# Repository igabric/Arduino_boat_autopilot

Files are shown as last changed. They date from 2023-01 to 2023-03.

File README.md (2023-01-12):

# ARDUINO AUTOPILOT FOR SMALL BOATS - short description

This project was created with the goal of creating a low-cost device for automatic navigation using the arduino mega microcontroller interface. The picture shows the finished device with all parts installed in the control box. 4 buttons installed on the control box, 1 rotary encoder and a remote control with 4 buttons are used to set and control the device. Steering is provided by the use of a stepper motor and a threaded rod, which enables the steering wheel to be turned by approximately 5 degrees in each direction.



The power supply of the microcontroller and the stepper motor driver are separate. The main power source is the ship's batteries, which are charged using photovoltaic panels. The voltage on the accumulators is between 13 and 14 V which is fine for the stepper motor driver, but too high for the arduino microcontroller. Therefore, powermodule DC-DC 15-80 to 12V step-down power supply converter is used to power the microcontroller. Since the stepper motor driver is built into the control box, the heatsink part faces outwards to promote heat dissipation and reduce the heating of the microcontroller. The temperature in the control box is continuously controlled using a thermistor. In the event that the temperature exceeds a critical value (which can be adjusted in the device settings), an alarm is triggered and the operation of the stepper motor is disabled.The parts installed in the control box are shown in the picture:



# Settings and device management are achieved through the menu system shown in the images below.

## Init menu layout
Used for the initial positioning of the steering wheel and to setting the system.



## Main manu layout
Used for the function of anchoring, manual control and automatic control of the boat.



# Programming Arduino 

## Program flow diagrams
The simplified flow charts shown below are only a general indication of how the program works. The program modules contains a lot of details that significantly affect the functionality of the device.
  
### ** Main program flow diagram: **


### ** Initialization flow diagram: **


### ** Flow diagram for "manually" setting the neutral position of the rudder: **
Since the use of encoders is not provided for determining the initial position of the rudder, it is necessary to "manually" adjust the neutral position of the rudder before starting the automatic operation of the autopilot. 
  


### ** Flow diagram for system parameter settings: **
Note: The program enables the setting of more system parameters than shown in the flowchart.


### ** Flow diagram for autopilot main menu: **
The main menu consists of six possible choices, two of which are hidden. The most important functionalities are navigation according to the given course and navigation according to the given destination. Applying navigation to a set course does not take into account drift due to wind and sea currents, making the final destination unreliable. In this case, the autopilot tries to maintain the given course. By applying navigation to the destination (set longitude and latitude of the destination), the course is corrected during navigation, i.e. calculated based on the current position and the position of the destination. This method of navigation is reliable, and the error depends on the precision of the GPS device (for cheaper devices, it is of the order of 10 m).
The next functionality is the anchoring function. By calling this function at the moment of lowering the anchor, the current GPS position is recorded and the permitted deviation from the current position can be entered. If during the stay on the anchor there is a greater deviation than allowed (the anchor has loosened), an alarm (buzzer) is activated.
By starting the microcontroller, multiple points of interest (POIs) stored on the SD card are loaded. The program enables the entry of one custom POI that can be used within the navigation function to the destination (fourth function in the main menu).
The fifth hidden function refers to the manual control of the boat, which is achieved by pressing the button of the rotary encoder. Calling this function enables control using the buttons on the control box or using the remote control.
The sixth function refers to the return to the home menu.



### ** Flow diagram for anchoring function: **
Starting the anchoring function automatically records the current GPS location. Then the input of the permitted deviation from the current position is requested. After that, monitoring of the position on the anchor is started. A circle is drawn on the screen, the radius of which represents the permissible deviation from the anchoring location (center point). The current position is plotted on the LCD screen and refreshed every 5 seconds. If the distance of the current location from the anchoring location is greater than the permitted deviation, an alarm is activated.


### ** Flow diagram for input custom POI coordinates: **
Custom POI can be entered by entering two digits at a time to speed up coordinate entry. Coordinates are entered in decimal notation. Each entry must be confirmed by pressing the button on the rotary encoder. The program provides for the input of coordinates with 6 decimal places, although the flow diagram shows the input of only 4 decimal places.



### ** Flow diagram for navigation to destination (point of interest): **
Navigation towards the desired destination is done by first choosing a destination from the available database stored on the SD card or a custom POI that has been previously defined. After selecting the destination, the current location is read and the course towards the destination is calculated. If the speed of the boat is higher than the minimum required, which is defined in the program settings, it is checked whether the deviation of the current course from the budget is greater than the allowed tolerance. If the course deviation is greater, the rudder is turned in the appropriate direction. The process is repeated after 5 seconds. If the deviation of the course from the budget is less than allowed, the rudder returns to the neutral position. In the loop there is also the possibility to return to the main menu. In this way, the maximum precision of the navigation path is ensured, regardless of the wind and sea currents, because the course is recalculated every 5 seconds ("course over ground").



### ** Flow diagram for navigation to desired course: **
Navigation towards the desired direction (course) starts with entering the numerical value of the desired course. After that, the current GPS position (previous position) is read. Then there is a pause of 5 seconds after which the new current GPS position (next position) is loaded. Based on the two read positions, the current exchange rate is calculated. If the speed of the boat is higher than the minimum required (defined in the system settings), the current and desired course are compared. If the deviation is greater, the rudder is turned in the appropriate direction. Then the next position is declared as the previous position and the loop is repeated. If the deviation is less than allowed, the rudder returns to the neutral position. In the loop, it is possible to return to the main menu.



### ** Flow diagram for manual control: **
Starting the menu for manual control is done by pressing the button on the rotary encoder. This makes it possible to turn the rudder using the buttons on the device housing or using the remote control. The upper two buttons are used to gradually turn the rudder to the left or right, while pressing either of the lower two buttons returns the rudder to the neutral position. In the loop, it is possible to return to the main menu.



### ** Used components: **
1. TB6600 Single Axis 4A Stepper Motor Microstep Driver 9~40V Micro-Step - 1Pcs
2. Nema 23 Stepper Motor 3Nm/1.9Nm/1.26Nm 4-lead 2.8A/4.2A - 1Pcs
3. Beitian BN-800 Dual Module with Antenna Compass HMC5883L - 1Pcs
4. Mini 12mm Waterproof Momentary ON/OFF Push Button Round Switch - 4Pcs
5. 12mm Metal Push Button Switch Waterproof LED Light Momentary Latching - 1Pcs
6. 24V / 12V to 5V 5A powermodule DC-DC step-down power supply converter - 1Pcs
7. 315MHz/433MHz 4Buttons RF Remote Control - 1Pcs
8. 4 Channel 433MHz RF Wireless Remote Control Learning Decoding Receiver Module - 1Pcs
9. 3.2 Inch MEGA2560 Display Module HX8357B 480x320 TFT LCD Screen  - 1Pcs
10. 40 pcs Dupont Cables M-F Jumper Breadboard Wire GPIO Ribbon for connecting TFT LCD with Arduino MEGA - 1Pcs
11. MEGA 2560 R3 Arduino komp. Mikrokontroller Board Atmel ATmega2560  - 1Pcs
12. Several Dupont Cables M-F, M-M, F-F Jumper Breadboard Wire for wiring
13. NTC 3950 Thermistor 100KOhm  - 1Pcs
14. Resistor 100kOhm - 1Pcs
15. KY-040 Rotary Encoder Module - 1Pcs

### ** Wiring diagram: **


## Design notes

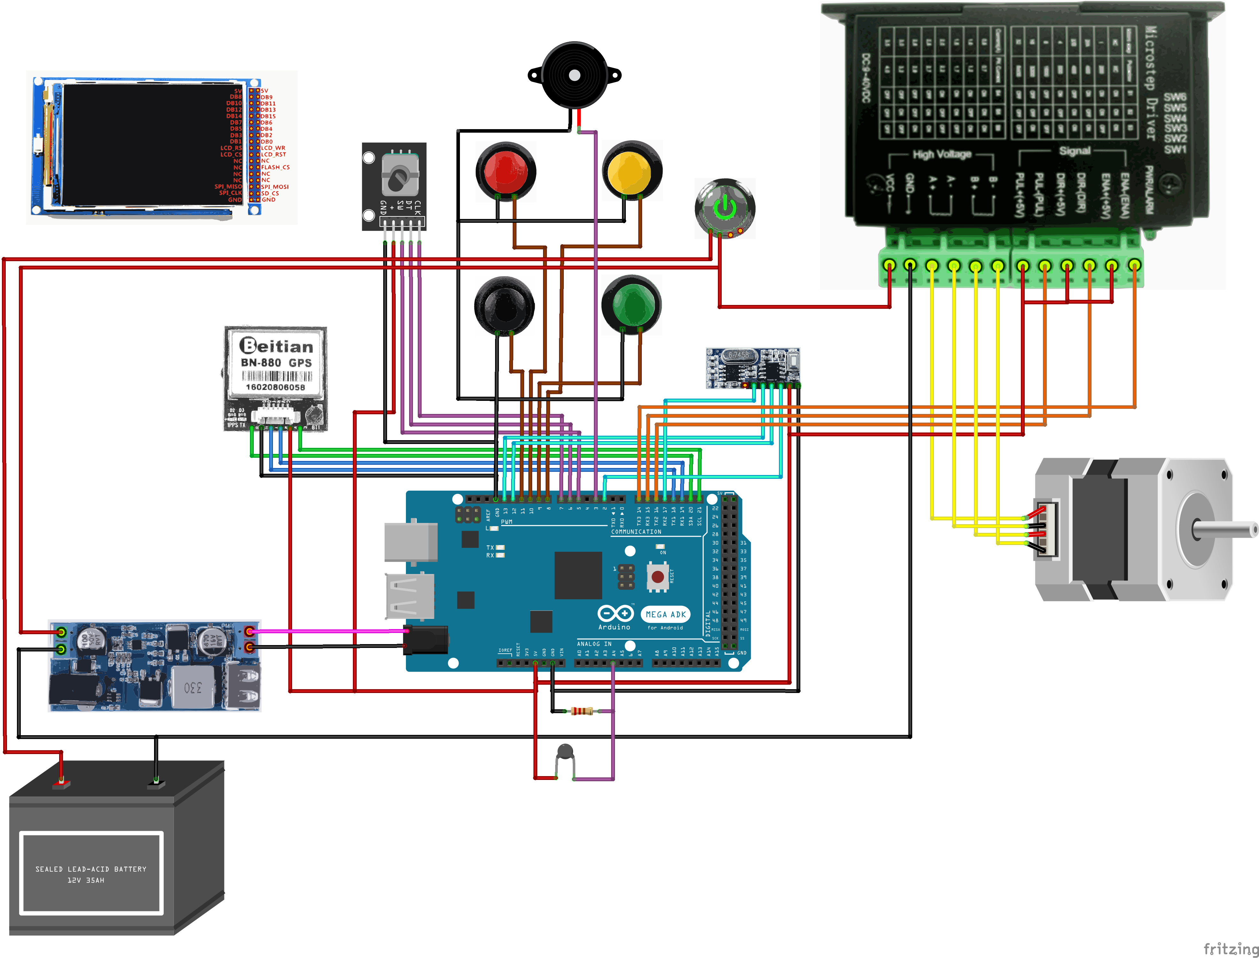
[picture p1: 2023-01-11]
Autopilot_shema.png

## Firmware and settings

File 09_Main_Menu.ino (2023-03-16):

void Screen_1_navigation(){
  int active_btn = 0;
  bool state = false;
  tft.fillScreen(TFT_BLACK);
  tft.drawRect(5, 5, 230, 150, TFT_YELLOW);
  tft.drawRect(245, 5, 230, 150, TFT_YELLOW);
  tft.drawRect(5, 165, 230, 150, TFT_YELLOW);
  tft.drawRect(245, 165, 230, 150, TFT_YELLOW);

  
  Set_Screen_1("Button 1", "Anchoring", 5, 5, false);
  Set_Screen_1("Button 2",  "Enter custom POI", 245, 5, false);
  Set_Screen_1("Button 3",  "Navigate by selected POI", 5, 165, false);
  Set_Screen_1("Button 4",  "Navigate by heading", 245, 165, false);
  TFT_print_entered_values();
  delay(1000);
  int prolaz_vrij = 0;
  while (true){
    prolaz_vrij += 1;
    if(prolaz_vrij == 2){
      temp = temperatura(); 
      tft.setTextColor(TFT_YELLOW, TFT_BLACK);
      tft.setCursor(410, 20, 4);
      tft.print(temp, 0);
      tft.setCursor(445, 20, 4);
      tft.print("C");
      prolaz_vrij = 0;
    }
    
    if(digitalRead(SW)== LOW){
      Manual_navigate();
    }
    if(digitalRead(PB_10p) == LOW and digitalRead(PB_1p) == LOW and digitalRead(PB_1n) == HIGH and digitalRead(PB_10n) == HIGH and digitalRead(SW)== HIGH){
      break;
    }
    if(digitalRead(PB_10n) == LOW){  
      Serial.println("Anchoring");
      if(active_btn == 1){
        state = 0; active_btn == 0;
        Set_Screen_1("Button 1", "Anchoring", 5, 5, false);
      }
      else if(active_btn == 2){
        Set_Screen_1("Button 2",  "Enter custom POI", 245, 5, false);
        Set_Screen_1("Button 1", "Anchoring", 5, 5, true);
        active_btn = 1; state = 1;
      }
      else if(active_btn == 3){
        Set_Screen_1("Button 3",  "Navigate by selected POI", 5, 165, false);
        Set_Screen_1("Button 1", "Anchoring", 5, 5, true);
        active_btn = 1; state = 1;
      }
      else if(active_btn == 4){
        Set_Screen_1("Button 4",  "Navigate by heading", 245, 165, false);
        Set_Screen_1("Button 1", "Anchoring", 5, 5, true);
        active_btn = 1; state = 1;
      }
      else{
        Set_Screen_1("Button 1", "Anchoring", 5, 5, true);
        active_btn = 1; state = 1;
      }
      delay(500);
    }
  if (digitalRead(PB_10n) == HIGH and digitalRead(PB_1n) == HIGH and digitalRead(PB_1p) == HIGH and digitalRead(PB_10p) == LOW and digitalRead(SW)== HIGH){
      Serial.println("Set POI");
      if(active_btn == 1){
        Set_Screen_1("Button 1", "Anchoring", 5, 5, false);
        Set_Screen_1("Button 2",  "Enter custom POI", 245, 5, true);
        active_btn = 2; state = 1;   
      }
      else if(active_btn == 2){
        state = 0; active_btn == 0;
        Set_Screen_1("Button 2",  "Enter custom POI", 245, 5, false);
      }
      else if(active_btn == 3){
        Set_Screen_1("Button 3",  "Navigate by selected POI", 5, 165, false);
        Set_Screen_1("Button 2",  "Enter custom POI", 245, 5, true);
        active_btn = 2; state = 1;
      }
      else if(active_btn == 4){
        Set_Screen_1("Button 4",  "Navigate by heading", 245, 165, false);
        Set_Screen_1("Button 2",  "Enter custom POI", 245, 5, true);
        active_btn = 2; state = 1;
      }
      else{
        Set_Screen_1("Button 2",  "Enter custom POI", 245, 5, true);
        active_btn = 2; state = 1;
      }
      delay(500);
    }
    if (digitalRead(PB_10n) == HIGH and digitalRead(PB_1n) == LOW and digitalRead(PB_1p) == HIGH and digitalRead(PB_10p) == HIGH and digitalRead(SW)== HIGH){
      Serial.println("Navigate by POI");
      if(active_btn == 1){
        Set_Screen_1("Button 1", "Anchoring", 5, 5, false);
        Set_Screen_1("Button 3",  "Navigate by selected POI", 5, 165, true);
        active_btn = 3; state = 1;   
      }
      else if(active_btn == 2){
        Set_Screen_1("Button 2",  "Enter custom POI", 245, 5, false);
        Set_Screen_1("Button 3",  "Navigate by selected POI", 5, 165, true);
        active_btn = 3; state = 1;
      }
      else if(active_btn == 3){
        state = 0; active_btn == 0;
        Set_Screen_1("Button 3",  "Navigate by selected POI", 5, 165, false);
      }
      else if(active_btn == 4){
        Set_Screen_1("Button 4",  "Navigate by heading", 245, 165, false);
        Set_Screen_1("Button 3",  "Navigate by selected POI", 5, 165, true);
        active_btn = 3; state = 1;
      }
      else{
        Set_Screen_1("Button 3",  "Navigate by selected POI", 5, 165, true);
        active_btn = 3; state = 1;
      }
      delay(500);
    }
    if (digitalRead(PB_10n) == HIGH and digitalRead(PB_1n) == HIGH and digitalRead(PB_1p) == LOW and digitalRead(PB_10p) == HIGH and digitalRead(SW)== HIGH){
      Serial.println("Navigate by heading");
      if(active_btn == 1){
        Set_Screen_1("Button 1", "Anchoring", 5, 5, false);
        Set_Screen_1("Button 4",  "Navigate by heading", 245, 165, true);
        active_btn = 4; state = 1;   
      }
      else if(active_btn == 2){
        Set_Screen_1("Button 2",  "Enter custom POI", 245, 5, false);
        Set_Screen_1("Button 4",  "Navigate by heading", 245, 165, true);
        active_btn = 4; state = 1;
      }
      else if(active_btn == 3){
        Set_Screen_1("Button 3",  "Navigate by selected POI", 5, 165, false);
        Set_Screen_1("Button 4",  "Navigate by heading", 245, 165, true);
        active_btn = 4; state = 1;
      }
      else if(active_btn == 4){
        state = 0; active_btn == 0;
        Set_Screen_1("Button 4",  "Navigate by heading", 245, 165, false);
      }
      else{
        Set_Screen_1("Button 4",  "Navigate by heading", 245, 165, true);
        active_btn = 4; state = 1;
      }
      delay(500);
    }
    
    if (state == 1){
      // CHOICE OF POIs BETWEEN OFFERED IN THE INTERNAL DATABASE
      if(active_btn == 1){ 
        Anchor_alarm();
        state = 0;
        Screen_1_navigation();
      }
      // ENTRY OF "CUSTOM" GEOGRAPHIC COORDINATES
      else if(active_btn == 2){
        // Enter custom POI coordinates
        number_of_POI = 26;
        pointArray[25] = "CUSTOM_POI";
        //Label(pointArray[arrLen], 200, 270, 4,"green");
        tft.setTextColor(TFT_YELLOW, TFT_BLACK);
        tft.setCursor(200, 270, 4);
        tft.print(pointArray[25]);
        rot_encoder_SET_CUSTOM_POI();
        longArray[25] = custom_POI_long;
        latArray[25] = custom_POI_lat;
         
        sign_custom_POI = true;
        state = 0;

        delay(1000);
        Screen_1_navigation();
      }
      // AUTOMATIC NAVIGATION by POINT OF INTEREST (POI)
      else if(active_btn == 3){
        // Navigate by selected POI 
        if (POI_selection != NULL){
          select_POI();
          state = 0;
          Autopilot_heading_POI(false);
          autopilot_ON = true;
          Navigate_by_POI();     
          delay(1000);
          Screen_1_navigation();
        }
        else{

          select_POI();         
          state = 0;
          autopilot_ON = true;
          Autopilot_heading_POI(false);
          Navigate_by_POI();     
          delay(1000);
          Screen_1_navigation();
        }
      }
      // AUTOMATIC NAVIGATION BY SELECTED HEADING
      else if(active_btn == 4){
        // Navigate by heading
        Autopilot_heading_POI(true);
        autopilot_ON = true;
        Autopilot(true);
        state = 0;
        Screen_1_navigation();
      }
    }
    delay(500);
  } 
  tft.fillScreen(TFT_BLACK);
}  


// ************************************************************************************************

//                                         Set_Screen_1 MODULE
//                                  SET ACTIVE BUTTON COLOUR ON SCREEN 1

// ************************************************************************************************
void Set_Screen_1(String text_btn, String description, int posx, int posy, bool active){
  if (active == true){
    tft.drawRect(posx, posy, 230, 150, TFT_WHITE);
    tft.setTextColor(TFT_WHITE, TFT_BLACK);
  }
  else{
    tft.drawRect(posx, posy, 230, 150, TFT_YELLOW);
    tft.setTextColor(TFT_RED, TFT_BLACK);
  }
  if (text_btn == "Button 1"){
    tft.fillCircle(posx + 115, posy + 40, 15, TFT_WHITE);
    tft.fillCircle(posx + 115, posy + 40, 12, TFT_RED);
  }
  else if (text_btn == "Button 2"){
    tft.fillCircle(posx + 115, posy + 40, 15, TFT_WHITE);
    tft.fillCircle(posx + 115, posy + 40, 12, TFT_YELLOW);
  }
  else if (text_btn == "Button 3"){
    tft.fillCircle(posx + 115, posy + 40, 15, TFT_WHITE);
    tft.fillCircle(posx + 115, posy + 40, 12, TFT_BLACK);
  }
  else if (text_btn == "Button 4"){
    tft.fillCircle(posx + 115, posy + 40, 15, TFT_WHITE);
    tft.fillCircle(posx + 115, posy + 40, 12, TFT_GREEN);
  }
  // tft.setCursor(posx + 30, posy + 50, 4);
  // tft.print(text_btn);
  tft.setCursor(posx + 30, posy + 80, 2);
  tft.print(description);
}
// ------------------------------------------------------------------------------------------------

// ************************************************************************************************

//                                    TFT_print_entered_values MODULE
//                               SHOW ON THE SCREEN 1 SELECTED/ENTERED VALUE 

// ************************************************************************************************
void TFT_print_entered_values(){
  if(custom_POI_long != NULL){
    tft.setTextColor(TFT_GREEN, TFT_BLACK);
    tft.setCursor(245 + 30, 5 + 100, 2);
    tft.print("Long:");
    tft.setCursor(245 + 30, 5 + 115, 2);
    tft.print("Lat:");
    tft.setTextColor(TFT_WHITE, TFT_BLACK);
    tft.setCursor(245 + 80, 5 + 100, 2);
    tft.print(custom_POI_long, 6); 
    tft.setCursor(245 + 80, 5 + 115, 2);
    tft.print(custom_POI_lat, 6);
  }
}
// ------------------------------------------------------------------------------------------------

void Manual_navigate(){
  digitalWrite(enablePin, HIGH); // enable stepper
  String buf1 = "000";
  tft.fillScreen(TFT_BLACK);
  tft.setTextColor(TFT_CYAN, TFT_BLACK);
  tft.setCursor(140, 40, 4);
  tft.println("MANUAL STEERING");
  tft.setCursor(20, 270, 4);
  tft.setTextColor(TFT_WHITE, TFT_BLACK);
  tft.println("Steering position:");
  drawRAW("kormilo_.raw", 215, 135, 50, 50);
  delay(1000);
  while (digitalRead(SW)== HIGH){
    tft.fillRect(270, 270, 50, 30, TFT_BLACK);
    buf1 = Leading_zero(STEPPER_MOTOR.getCurrentPositionInMillimeters(), 3);
    tft.setTextColor(TFT_YELLOW, TFT_BLACK);
    tft.setCursor(270, 270, 4);
    tft.print(buf1);
    if (digitalRead(PB_10p) == LOW and digitalRead(PB_1p) == HIGH and digitalRead(PB_1n) == HIGH and digitalRead(PB_10n) == HIGH and digitalRead(SW)== HIGH){
      // SET STEPPER CLOCKWISE
      sterring_positive();
    }
    else if(digitalRead(button1) == HIGH){
      // SET STEPPER COUNTERCLOCKWISE
      sterring_negative();
    }

    else if(digitalRead(button2) == HIGH){
      // SET STEPPER CLOCKWISE
      sterring_positive();
    }
    else if(digitalRead(PB_10p) == HIGH  and digitalRead(PB_1p) == HIGH and digitalRead(PB_1n) == HIGH and digitalRead(PB_10n) == LOW and  digitalRead(SW)== HIGH){
      // SET STEPPER COUNTERCLOCKWISE
      sterring_negative();
    }
    else if(digitalRead(PB_1p) == LOW or digitalRead(PB_1n) == LOW or digitalRead(button3) == HIGH or digitalRead(button4) == HIGH){
      tft.fillRect(220, 220, 40, 40, TFT_GREEN);
      // SET STEPPER NEUTRAL
      digitalWrite(enablePin, HIGH); // enable stepper
      temp = temperatura(); 
      STEPPER_MOTOR.moveToPositionInMillimeters(0);
      digitalWrite(enablePin, LOW); // disable stepper
      delay(500);
    }
    tft.fillTriangle(60, 160, 90, 140, 90, 180, TFT_BLACK);
    tft.fillTriangle(410, 160, 380, 140, 380, 180, TFT_BLACK);
    tft.fillRect(220, 220, 40, 40, TFT_BLACK);
    tft.setTextColor(TFT_BLACK, TFT_BLACK);
    tft.setCursor(135, 80, 4);
    tft.println("STEERING LIMIT !!!");
    digitalWrite(enablePin, LOW); // disable stepper
  }
  digitalWrite(enablePin, LOW); // disable stepper
  Screen_1_navigation();
}

void sterring_positive(){
  tft.fillTriangle(410, 160, 380, 140, 380, 180, TFT_GREEN);
  if(step_direction_positive == 1){
    if(STEPPER_MOTOR.getCurrentPositionInMillimeters()> -Max_steering_turning_deg){
      digitalWrite(enablePin, HIGH); // enable stepper
      temp = temperatura(); 
      STEPPER_MOTOR.moveRelativeInMillimeters(-10);
      // digitalWrite(enablePin, LOW); // disable stepper
    }
    else{
      tft.setTextColor(TFT_RED, TFT_BLACK);
      tft.setCursor(135, 80, 4);
      #ifdef DEBUG
        Serial.print("CurrentPositionInDegs: ");
        Serial.println(STEPPER_MOTOR.getCurrentPositionInMillimeters());
      #endif 
      tft.println("STEERING LIMIT !!!");
      delay(500);
    }
  }
  else{
    if(STEPPER_MOTOR.getCurrentPositionInMillimeters()<Max_steering_turning_deg){
      digitalWrite(enablePin, HIGH); // enable stepper
      temp = temperatura(); // 
      STEPPER_MOTOR.moveRelativeInMillimeters(10);
      // digitalWrite(enablePin, LOW); // disable stepper
    }
    else{
      tft.setTextColor(TFT_RED, TFT_BLACK);
      tft.setCursor(135, 80, 4);
      #ifdef DEBUG
        Serial.print("CurrentPositionInDegs: ");
        Serial.println(STEPPER_MOTOR.getCurrentPositionInMillimeters());
      #endif 
      tft.println("STEERING LIMIT !!!");
      delay(500);
    }
  }
}

void sterring_negative(){
  tft.fillTriangle(60, 160, 90, 140, 90, 180, TFT_GREEN);
  if(step_direction_positive == 1){
    if(STEPPER_MOTOR.getCurrentPositionInMillimeters()<Max_steering_turning_deg){
      digitalWrite(enablePin, HIGH); // enable stepper
      temp = temperatura();
      STEPPER_MOTOR.moveRelativeInMillimeters(10);
      // digitalWrite(enablePin, LOW); // disable stepper
    }
    else{
      tft.setTextColor(TFT_RED, TFT_BLACK);
      tft.setCursor(135, 80, 4);
      #ifdef DEBUG
        Serial.print("CurrentPositionInDegs: ");
        Serial.println(STEPPER_MOTOR.getCurrentPositionInMillimeters());
      #endif 
      tft.println("STEERING LIMIT !!!");
      delay(500);
    }
  }
  else{
    if(STEPPER_MOTOR.getCurrentPositionInMillimeters()> -Max_steering_turning_deg){
      digitalWrite(enablePin, HIGH); // enable stepper
      temp = temperatura();
      STEPPER_MOTOR.moveRelativeInMillimeters(-10);
      // digitalWrite(enablePin, LOW); // disable stepper
    }    
    else{
      tft.setTextColor(TFT_RED, TFT_BLACK);
      tft.setCursor(135, 80, 4);
      #ifdef DEBUG
        Serial.print("CurrentPositionInDegs: ");
        Serial.println(STEPPER_MOTOR.getCurrentPositionInMillimeters());
      #endif 
      tft.println("STEERING LIMIT !!!");
      delay(500);
    }
  }  
}

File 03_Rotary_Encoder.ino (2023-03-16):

// ************************************************************************************************

//                                      ROTARY ENCODER MODULE
//                               SETTING VALUE USING ROTARY ENCODER

// ************************************************************************************************
float rot_encoder(float set_value, int dec_plc, int max_val, String text) {
  unsigned long lastButtonPress = millis();
  float izlazna_velicina;
  int counter = 0;
  izlazna_velicina = set_value;
  char buf1[8];
  int currentStateCLK;
  Label(text,10,110,4,"green"); 
  SET_HDG(float(izlazna_velicina));
  while( true ) {
    currentStateCLK = digitalRead(CLK);  // Read the current state of CLK
    if (currentStateCLK != lastStateCLK  && currentStateCLK == 1) {
      if (digitalRead(DT) != currentStateCLK) {
        counter ++;
        int heading = int(izlazna_velicina + counter/pow(10,dec_plc));
        if (heading > max_val- 1){
          counter -= max_val;
        }
        SET_HDG(float(izlazna_velicina + counter/pow(10,dec_plc)));
      } else {
        counter --;
        int heading = int(izlazna_velicina + counter/pow(10,dec_plc));
        if (heading < 0){
          counter += max_val;
        }
        SET_HDG(float(izlazna_velicina + counter/pow(10,dec_plc)));
      }
    }
    lastStateCLK = currentStateCLK;
  
    int btnState = digitalRead(SW);
    if (btnState == LOW) {
      if (millis() - lastButtonPress > 50) {
        izlazna_velicina += counter/pow(10,dec_plc);
        break;
      }
      lastButtonPress = millis();
    }
  }
  Label(text,10,110,4,"black"); 
  delay(1);
  return izlazna_velicina;
}
// ------------------------------------------------------------------------------------------------

// ************************************************************************************************

//                                      SETTING ACTIVE POI MODULE
//                               SETTING ACTIVE POI USING ROTARY ENCODER

// ************************************************************************************************
int rot_encoder_POI() {
  unsigned long lastButtonPress = millis();
  int count = 0;
  int currentStateCLK;
  int x1 = 220;  int x2 = 300;  int y1 = 220;
  Label("POI:",220, 160, 4,"black"); Label("POI SETTING:",220, 160, 4,"green"); 
  while( true ) {
    currentStateCLK = digitalRead(CLK);  // Read the current state of CLK
    if (currentStateCLK != lastStateCLK  && currentStateCLK == 1) {
      if (digitalRead(DT) != currentStateCLK) {
        count --;
        
        if (count < 0){
          Label(pointArray[0],220, 190, 4,"black");
          Label(String(latArray[0],6),x1, y1, 2,"black");
          Label(String(longArray[0],6),x2, y1, 2,"black");
          count += number_of_POI;
        }
        Label(pointArray[count+1],220, 190, 4,"black"); Label(pointArray[count],220, 190, 4,"white");
        Label(String(latArray[count+1],6),x1, y1, 2,"black"); Label(String(latArray[count],6),x1, y1, 2,"white");
        Label(String(longArray[count+1],6),x2, y1, 2,"black"); Label(String(longArray[count],6),x2, y1, 2,"white");
      } else {
        count ++;
        if (count > number_of_POI - 1){
          Label(pointArray[number_of_POI - 1],220, 190, 4,"black");
          Label(String(latArray[number_of_POI - 1],6),x1, y1, 2,"black");
          Label(String(longArray[number_of_POI - 1],6),x2, y1, 2,"black");
          count -= number_of_POI;
        }
        Label(pointArray[count-1],220, 190, 4,"black"); Label(pointArray[count],220, 190, 4,"white"); 
        Label(String(latArray[count-1],6),x1, y1, 2,"black"); Label(String(latArray[count],6),x1, y1, 2,"white");
        Label(String(longArray[count-1],6),x2, y1, 2,"black"); Label(String(longArray[count],6),x2, y1, 2,"white");
      }
    }
    lastStateCLK = currentStateCLK;
    int btnState = digitalRead(SW);
    if (btnState == LOW) {
      if (millis() - lastButtonPress > 50) {
        break;
      }
      lastButtonPress = millis();
    }
  }
  Label("POI SETTING:",220, 160, 4,"black"); Label("POI:",220, 160, 4,"cyan"); 
  return count;
}
// ------------------------------------------------------------------------------------------------

// ************************************************************************************************

//                                      POI SELECT MODULE
//                               SELECT ACTIVE POI USING ROTARY ENCODER

// ************************************************************************************************
int select_POI() {
  tft.fillScreen(TFT_BLACK);
  unsigned long lastButtonPress = millis();
  int count = 0;
  int currentStateCLK;
  Label("POI SELECT (use rotary encoder):",10, 100, 4,"green"); 
  while( true ) {
    currentStateCLK = digitalRead(CLK);  // Read the current state of CLK
    if (currentStateCLK != lastStateCLK  && currentStateCLK == 1) {
      if (digitalRead(DT) != currentStateCLK) {
        count --;
        
        if (count < 0){
          Label(pointArray[0],100, 200, 4,"black");
          Label(String(latArray[0],6),100, 250, 4,"black");
          Label(String(longArray[0],6),250, 250, 4,"black");
          count += number_of_POI;
        }
        Label(pointArray[count+1],100, 200, 4,"black"); Label(pointArray[count],100, 200, 4,"white");
        Label(String(latArray[count+1],6),100, 250, 4,"black");Label(String(latArray[count],6),100, 250, 4,"white");
        Label(String(longArray[count+1],6),250, 250, 4,"black");Label(String(longArray[count],6),250, 250, 4,"white");
      } else {
        count ++;
        if (count > number_of_POI - 1){
          Label(pointArray[number_of_POI - 1],100, 200, 4,"black");
          Label(String(latArray[number_of_POI - 1],6),100, 250, 4,"black");
          Label(String(longArray[number_of_POI - 1],6),250, 250, 4,"black");
          count -= number_of_POI;
        }
        Label(pointArray[count-1],100, 200, 4,"black"); Label(pointArray[count],100, 200, 4,"white"); 
        Label(String(latArray[count-1],6),100, 250, 4,"black");Label(String(latArray[count],6),100, 250, 4,"white");
        Label(String(longArray[count-1],6),250, 250, 4,"black");Label(String(longArray[count],6),250, 250, 4,"white");
      }
    }
    lastStateCLK = currentStateCLK;
    int btnState = digitalRead(SW);
    if (btnState == LOW) {
      if (millis() - lastButtonPress > 50) {
        break;
      }
      lastButtonPress = millis();
    }
  }
  POI_selection = count;
  Label("OK",350, 200, 4,"yellow");
  delay(1000);
}
// ------------------------------------------------------------------------------------------------

// ************************************************************************************************

//                                         SET CUSTOM POI MODULE
//                               SETTING CUSTOM POI LONGITUDE AND LATITUDE
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
